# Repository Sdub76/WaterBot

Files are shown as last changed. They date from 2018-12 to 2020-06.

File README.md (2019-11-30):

# WaterBot 2
Christmas Tree Watering Robot 
Tree Watering Robot created to keep the Christmas tree wet without having to refill it everyday.  

## Features
1.  Monitor tree water level
2.  Monitor supply water level
3.  Pump water when tree water is low
4.  Only allow a maximum pump-on period per pumping session to avoid a HW or SW bug flooding the living room
5.  Give visual indication (via light on tree) that the pump is running
6.  Give visual indication (via light on tree) that the supply is empty
7.  Give visual indication (via light on tree) that there's a hardware fault
9.  Provide local debugging via OLED screen 
10.  (TBD) Log data via MQTT (Wi-fi) to see if things are working

Version 2 description TBD - Breadboard replaced by PCB, Crappy soil moisture sensor replaced with IR water sensor

## Shopping List
* TBD

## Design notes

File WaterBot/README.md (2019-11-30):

# WaterBot
ESP8266-based Tree Water Monitor
Tree Watering Robot created to keep the Christmas tree wet without having to refill it everyday.  

(https://youtu.be/NFjdOTcmyZQ "Click to Play in YouTube")

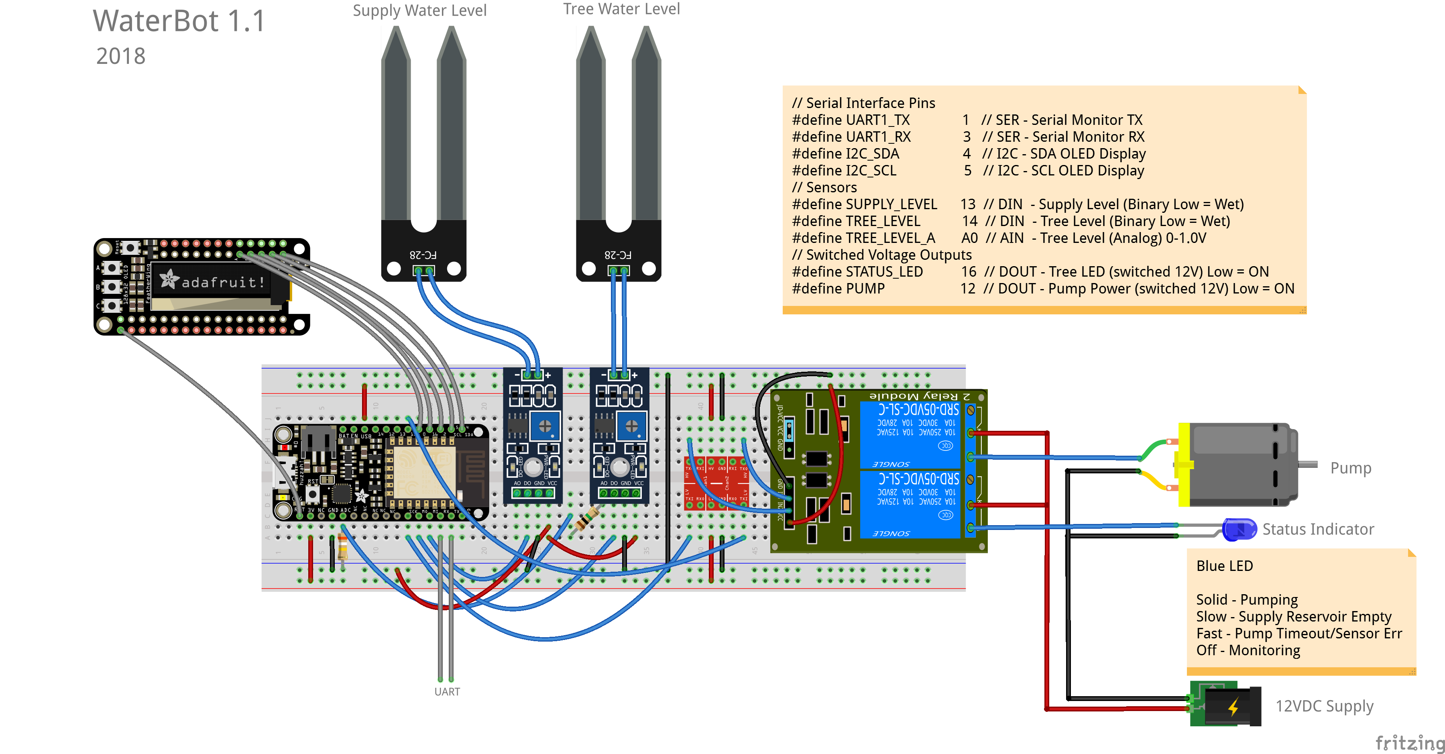
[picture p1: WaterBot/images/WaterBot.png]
Fritizing Image


## Features
1.  Monitor tree water level
2.  Monitor supply water level
3.  Pump water when tree water is low
4.  Only allow a maximum pump-on period per pumping session to avoid a HW or SW bug flooding the living room
5.  Give visual indication (via light on tree) that the pump is running
6.  Give visual indication (via light on tree) that the supply is empty
7.  Give visual indication (via light on tree) that there's a hardware fault
8.  (Disabled) Only turn on tree sensors when periodic readings are taking place to avoid sensor degradation via electrolysis
9.  Provide local debugging via OLED screen 
10.  (TBD) Log data via MQTT (Wi-fi) to see if things are working

NOTE: The original intent was to excite the tree level sensors with a digital output pin of the controller, so that the "on" time would be minimized, thus prolonging the life of the sensor probes.  The sensor probes electrolyze the water and erode the contacts when they're energized... thus you should only turn them on for a brief period if you're only taking periodic readings.  Unfortunately, I didn't have any spare GPIO pins on the ESP that weren't also used for bootloader control, so I commented out this code.  I suppose the sensors will work fine for a few weeks during the holiday season :)

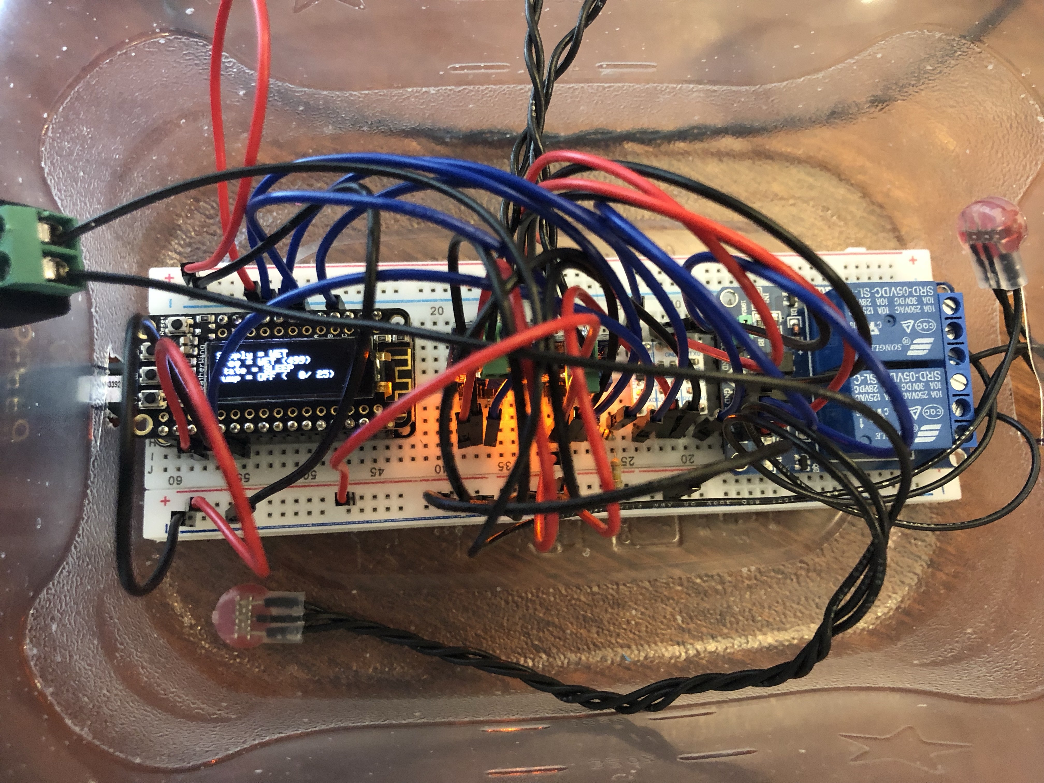
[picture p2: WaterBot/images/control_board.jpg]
Control Board

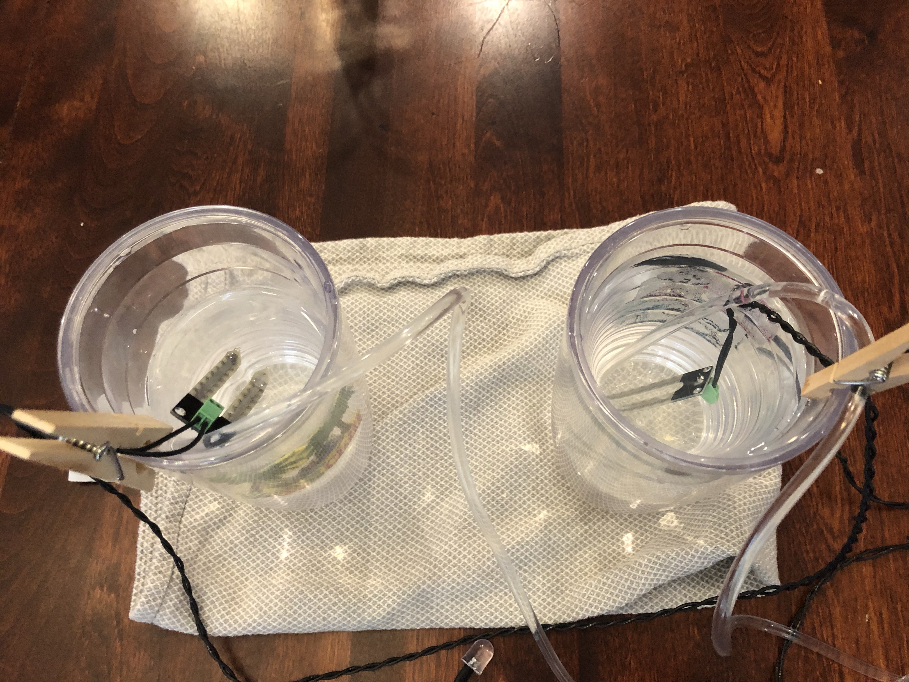
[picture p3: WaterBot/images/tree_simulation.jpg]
Tree Simulation


## Shopping List
* 1	Adafruit Feather HUZZAH ESP8266	part # [Adafruit #2821](https://www.adafruit.com/product/2821)
* 1	Adafruit OLED FeatherWing	part # [Adafruit #2900](https://www.adafruit.com/product/2900)
* 2	FC-28 Soil Hygrometer Module/Probe (http://a.co/d/3ILjnXG)
* 1	12VDC Diaphram pump	(http://a.co/d/7KirTrF)
* 1	Logic Level Converter	(https://www.microcenter.com/product/476364/velleman-33v-5v-ttl-logic-level-converter-module)
* 1	2-Channel 5v Relay Module (http://a.co/d/bQ4BVRI)
* 1	12VDC Power Supply (http://a.co/d/5liJUTH)
* 1	Blue (430nm) LED
* 1 220Ω Resitor for LED
* 1	1MΩ Resistor for Analog input voltage divider
* 1	390kΩ Resistor for Analog input voltage divider

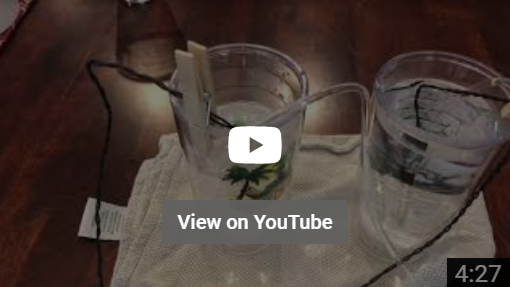
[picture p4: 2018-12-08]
WaterBot/images/youtube_thumb.png

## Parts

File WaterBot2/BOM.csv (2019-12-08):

RefDes | Quantity | Manufacturer | Function | Cost
C3 | 1 | CAP400 10uF | Power decouple | $0.04
C4 | 1 | CAP400 10uF | Power decouple | $0.04
C6 | 1 | CAP400 100nF | Sensor decouple | $0.04
C7 | 1 | CAP400 100nF | Sensor decouple | $0.04
C8 | 1 | CAP400 100nF | Sensor decouple | $0.04
D1 | 1 | LED Red | Power LED | $0.25
D2 | 1 | LED Blue | Tree Switch LED | $0.25
D3 | 1 | LED Blue | Tree Sensor LED1 | $0.25
D4 | 1 | LED Blue | Tree Sensor LED2 | $0.25
D5 | 1 | LED Blue | Tree Sensor LED3 | $0.25
D6 | 1 | LED Blue | Tree Sensor LED4 | $0.25
D7 | 1 | LED Blue | Supply Switch LED | $0.25
J1 | 1 | HDR-1x6 | Pro mini FTDI opt.
J2 | 1 | Molex 395021006 | SPI LED out | $1.40
J3 | 1 | Molex 395021002 | Lamp conn | $0.58
J4 | 1 | HDR-1x3 | Lamp relay out opt.
J5 | 1 | HDR-1x3 | Pump relay out opt.
J6 | 1 | Molex 395021002 | Pump conn | $0.58
J7 | 1 | Molex 395021003 | Supply switch in | $0.78
J8 | 1 | CUI PJ-002A | 12V barrel jack | $0.70
J9 | 1 | Molex 395021003 | Tree Sensor in | $0.78
J10 | 1 | Molex 395021002 | 12V in opt. | $0.58
J11 | 1 | Molex 395021003 | Tree Switch in | $0.78
J12 | 1 | HDR-1x4 | Relay control opt.
M1 | 1 | ARDUINO-PRO-MINI-5.0V | Control CPU | $9.95
MS1 | 1 | Adafruit featherwing ESP8266 | Monitoring CPU | $19.95
R1 | 1 | RES400 (220 Ohm) | 5V Power LED Res | $0.10
R2 | 1 | RES400 (220 Ohm) | Tree Switch LED Res | $0.10
R3 | 1 | RES400 (220 Ohm) | Tree Sensor LED1 Res | $0.10
R4 | 1 | RES400 (220 Ohm) | Tree Sensor LED2 | $0.10
R5 | 1 | RES400 (220 Ohm) | Tree Sensor LED3 | $0.10
R6 | 1 | RES400 (220 Ohm) | Tree Sensor LED4 | $0.10
R10 | 1 | RES400 (220 Ohm) | Supply Switch LED | $0.10
U1 | 1 | 2SRD Relay Module | Mechanical relays | $1.86
U2 | 1 | LM3940 | 5->3.3V regulator | $1.63
U3 | 1 | 4ch i2c logic level module | 5<->3.3V level conv | $2.95
U4 | 1 | 78SRinv_horiz | 12->5V regulator | $4.30
 | 1 | WaterBot 2.0 PCB | PCB | $1.88
 | 1 | 12V Diaphram Pump | Water pump | $7.68
 | 1 | Water level sensor (IR) | Tree level sensor | $7.67
 | 1 | Water level switch (IR) | Tree level switch | $2.60
 | 1 | Water level switch (IR) | Water supply switch | $2.60
 | 1 | Adafruit featherwing OLED |  | $14.95
 | 1 | 12VDC power supply |  | $10.98
 | 37 |  |  | $97.82

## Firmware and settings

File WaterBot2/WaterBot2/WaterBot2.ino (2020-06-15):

/* WaterBot2
 *
 * Version 2.0 of Tree Watering Robot
 *       
 * Tree watering system
 * 
 * Place supply switch at bottom of water tank
 * Place Tree switch at level you wwant watering to begin
 * Place Tree level sensor in stand's float hole
 * 
 * If tree switch is higher than level sernsor, error will be reported
 * If tree switch is lower than level sensor, pump won't run until both are satisfied,
 *    but risk of pump timing out of it runs too long, since water level is very low.  
 *    Care must be taken to not allow water level to get undesirably low.
 *    
 * LCD displays and ESP8266 are optional
 * 
 * Water Level Sensor
 * https://www.amazon.com/gp/product/B07BFPP4TQ/ref=ppx_yo_dt_b_asin_title_o01_s00?ie=UTF8&psc=1
 * Water Switch
 * https://www.amazon.com/gp/product/B0811GRVJH/ref=ppx_yo_dt_b_asin_title_o01_s00?ie=UTF8&psc=1
 * Water Pump
 * https://www.amazon.com/gp/product/B0744FWNFR/ref=ppx_yo_dt_b_search_asin_title?ie=UTF8&psc=1
 * 
 * Issues: Pump needs flyback diodes
 * 
 */
#include <FreqMeasure.h>
#include "TimedBlink.h"



//PIN DEFINITIONS
#define PIN_SERIAL_TX      0
#define PIN_SERIAL_RX      1

#define PIN_SPI_MOSI      11
#define PIN_SPI_MISO      12
#define PIN_SPI_SCK       13
#define PIN_SPI_SS        17

#define PIN_TREE_SENSOR   14
#define PIN_LEVEL_SENSOR   8
#define PIN_SUPPLY_SENSOR  7

#define PIN_TREE_LED       2
#define PIN_LEVEL1_LED     6
#define PIN_LEVEL2_LED     5 
#define PIN_LEVEL3_LED     4
#define PIN_LEVEL4_LED     3
#define PIN_SUPPLY_LED     9

#define PIN_PUMP          15
#define PIN_LAMP          16

//Sensor characteristics (Hz)
#define WATER_LEVEL_0 20
#define WATER_LEVEL_1 50
#define WATER_LEVEL_2 100
#define WATER_LEVEL_3 200
#define WATER_LEVEL_4 400

//States
int     SupplyState = 0;
int     TreeState = 0;
#define SENSOR_WET 0
#define SENSOR_DRY 1
#define SENSOR_ERR 2

int     PumpState = 0;
#define PUMP_OFF 0
#define PUMP_ON  1
#define PUMP_ERR 2

//Other parameters
#define AVERAGE_LENGTH 30  // Number of points to average for frequnecy calc
#define PUMP_MAXTIME   10  // Number of seconds to allow pump to run

double sum = 0;
int count = 0;
double frequency = 0;
unsigned long prev_time_freq = 0;
unsigned long prev_time_ser = 0;

//Inputs
int SupplySwitch = 0;
int TreeSwitch = 0;
unsigned long TreeLevel = 0;

// TIming state vars
unsigned long current_time = 0;
double timeout = 0;
double PumpStart = 0;

TimedBlink level1_led(PIN_LEVEL1_LED);
TimedBlink level2_led(PIN_LEVEL2_LED);
TimedBlink level3_led(PIN_LEVEL3_LED);
TimedBlink level4_led(PIN_LEVEL4_LED);
TimedBlink status_lamp(PIN_LAMP);

void setup() {

  Serial.begin(57600);
  Serial.println("Serial Initialized");

  // Intialize Inputs
  pinMode(PIN_TREE_SENSOR,INPUT);
  pinMode(PIN_LEVEL_SENSOR,INPUT);
  pinMode(PIN_SUPPLY_SENSOR,INPUT_PULLUP);

  // Intialize Outputs
  pinMode(PIN_TREE_LED,OUTPUT);
  pinMode(PIN_LEVEL1_LED,OUTPUT);
  pinMode(PIN_LEVEL2_LED,OUTPUT);
  pinMode(PIN_LEVEL3_LED,OUTPUT);
  pinMode(PIN_LEVEL4_LED,OUTPUT);
  pinMode(PIN_SUPPLY_LED,OUTPUT);
  pinMode(PIN_PUMP,OUTPUT);
  pinMode(PIN_LAMP,OUTPUT);
  level1_led.blink(50,50);
  level2_led.blink(50,50);
  level3_led.blink(50,50);
  level4_led.blink(50,50);
  
  FreqMeasure.begin();

  timeout = AVERAGE_LENGTH/(WATER_LEVEL_0*0.9);

}


void loop() {

  current_time = millis();

  ReadInputs();

  UpdateStates();

  WriteOutputs();

  UpdateDisplays();
  
  LogData();

  if ((current_time - prev_time_ser) > 2000) {

    DebugOutputs();
    prev_time_ser = current_time;
  }

}


void ReadInputs() {
  //Read Sensors
  
  SupplySwitch = digitalRead(PIN_SUPPLY_SENSOR);
  
  TreeSwitch = digitalRead(PIN_TREE_SENSOR);

  if (FreqMeasure.available()) {
    // average several reading together
    sum = sum + FreqMeasure.read();
    count = count + 1;
    if (count > AVERAGE_LENGTH) {
      // Reset timer
      prev_time_freq = current_time;
      frequency = FreqMeasure.countToFrequency(sum / count);
      sum = 0;
      count = 0;
      TreeLevel = 0;
      if (frequency > (WATER_LEVEL_0*0.9)) TreeLevel++;
      if (frequency > (WATER_LEVEL_1*0.9)) TreeLevel++;
      if (frequency > (WATER_LEVEL_2*0.9)) TreeLevel++;
      if (frequency > (WATER_LEVEL_3*0.9)) TreeLevel++;
      if (frequency > (WATER_LEVEL_4*0.9)) TreeLevel++;
    }
  }
//  if ((current_time - prev_time_freq) > timeout) {
//     TreeLevel = 0;
//     Serial.println("timeout");
//  }

}

void UpdateStates() {
  //Update States
  
  if (SupplySwitch == 0) {
    SupplyState = SENSOR_WET; // Low = Wet
  } else {
    SupplyState = SENSOR_DRY;
  }

  // Fuse TreeSwitch and TreeLevel into TreeState
  // ToDo: Add hysteresis
  if (TreeLevel == 0) {         // Sensor Timeout
    TreeState = SENSOR_ERR; 
  } else if (TreeSwitch == 0) { // Low = Wet (regardless of level sensor)
    TreeState = SENSOR_WET; 
  } else if (TreeLevel < 5) {  // Sensor Less than full and Switch = Dry
    TreeState = SENSOR_DRY; 
  } else {
    TreeState = SENSOR_ERR;   // Sensor Full & Switch Dry conflict -- Bad switch placement?
  }
  // Fuse TreeState and SwitchState into PumpState
  switch (PumpState) {
    case PUMP_OFF :
      if ((TreeState == SENSOR_DRY) && (SupplyState == SENSOR_WET)) {
        PumpStart = current_time; // Record pumping start time
        PumpState = PUMP_ON;
      }
      break;
    
    case PUMP_ON :
      // If TreeState or Supply State change, stop pumping
      if ((TreeState != SENSOR_DRY) || (SupplyState != SENSOR_WET)) {
        PumpState = PUMP_OFF;
      }
      
      if ((current_time - PumpStart) > PUMP_MAXTIME*1000) {
        PumpState = PUMP_ERR;
      }
      break;

    case PUMP_ERR :
      // Do nothing until power cycle
      // Todo: Add auto-reset sequence? Allow pumping as long as positive level progress being made?
    break;
  }
}

void WriteOutputs() {
  // Update Pump output
  if (PumpState == PUMP_ON) {
    digitalWrite(PIN_PUMP,false);
  } else {
    digitalWrite(PIN_PUMP,true);
  }

  // Update remote status lamp (in order of importance)
  // Note relay is active low, so "on" is really "off" in the blink routine
  //
  // Fast Blink = Sensor Error (Either Level=0Hz or Switch Dry while Level OK)
  // On Blip = Pump Lockout (Pump ran too long)
  // Off Blip = Supply Empty
  // Slow Blink = Pump On
  // On = Standby
  if (TreeState == SENSOR_ERR) {
    status_lamp.blink(50,50); 
  } else if (PumpState == PUMP_ERR) {
    status_lamp.blink(2000,50);
  } else if (SupplyState == SENSOR_DRY) {
    status_lamp.blink(50,2000);
  } else if (PumpState == PUMP_ON) {
    status_lamp.blink(1000,1000);
  } else {
    status_lamp.on();
  }
  
  // Update LEDs
  if (SupplySwitch == SENSOR_WET) {
    digitalWrite(PIN_SUPPLY_LED,true);
  } else {
    digitalWrite(PIN_SUPPLY_LED,false);
  }
  
  if (TreeSwitch == SENSOR_WET) {
    digitalWrite(PIN_TREE_LED,true);
  } else {
    digitalWrite(PIN_TREE_LED,false);
  }
  
  switch (TreeLevel) {
    case 0:
      level1_led.blink();
      level2_led.blink();
      level3_led.blink();
      level4_led.blink();
      break;
    case 1:
      level1_led.off();
      level2_led.off();
      level3_led.off();
      level4_led.off();
      break;
    case 2:
      level1_led.off();
      level2_led.off();
      level3_led.off();
      level4_led.on();
      break;
    case 3:
      level1_led.off();
      level2_led.off();
      level3_led.on();
      level4_led.on();
      break;
    case 4:
      level1_led.off();
      level2_led.on();
      level3_led.on();
      level4_led.on();
      break;
    case 5:
      level1_led.on();
      level2_led.on();
      level3_led.on();
      level4_led.on();
      break;
  }

}

void UpdateDisplays() {
  //ToDo: Drive I2C display directly -OR- Send to ESP8266 via UART
  //ToDo: Send SPI LCD commands (Alternative to lamp... 2020 enhancement)
}

void LogData() {
  //ToDo: Send data to ESP8266 for MQTDD logging (2020 enhancement)
}

void DebugOutputs() {

  Serial.println("==INPUTS==");
  Serial.print(" SupplySwitch = ");
  switch (SupplySwitch) {
    case SENSOR_WET : 
    Serial.println("WET");
    break;

    case SENSOR_DRY : 
    Serial.println("DRY");
    break;
    
    case SENSOR_ERR : 
    Serial.println("ERROR");
    break;
  }
  Serial.print(" TreeSwitch = ");
  switch (TreeSwitch) {
   case SENSOR_WET : 
    Serial.println("WET");
    break;

    case SENSOR_DRY : 
    Serial.println("DRY");
    break;
    
    case SENSOR_ERR : 
    Serial.println("ERROR");
    break;
  }
  Serial.print(" TreeLevel = ");
  Serial.print(TreeLevel);
  Serial.print(" (");
  Serial.print(frequency);
  Serial.println("Hz)");

  Serial.println("==STATES==");
  Serial.print(" SupplyState = ");
  switch (SupplyState) {
    case SENSOR_WET : 
    Serial.println("WET");
    break;

    case SENSOR_DRY : 
    Serial.println("DRY");
    break;
    
    case SENSOR_ERR : 
    Serial.println("ERROR");
    break;
  }
  Serial.print(" TreeState = ");
  switch (TreeState) {
    case SENSOR_WET : 
    Serial.println("WET");
    break;

    case SENSOR_DRY : 
    Serial.println("DRY");
    break;
    
    case SENSOR_ERR : 
    Serial.println("ERROR");
    break;
  }
  Serial.print(" PumpState = ");
  switch (PumpState) {
    case PUMP_OFF : 
    Serial.println("OFF");
    break;

    case PUMP_ON : 
    Serial.print("ON (");
    Serial.print((current_time-PumpStart)/1000);
    Serial.println("s)");
    break;
    
    case PUMP_ERR : 
    Serial.println("ERROR");
    break;
  }
  
  Serial.println("");
  
}

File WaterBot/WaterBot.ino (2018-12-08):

// WaterBot
// Christmas Tree Watering Bot
//  

#include <SPI.h>
#include <Wire.h>
#include <Adafruit_GFX.h>
#include <Adafruit_SSD1306.h>

/////////////////////////
// Macro Definition
/////////////////////////
// Printing with stream operator
template<class T> inline Print& operator <<(Print &obj,     T arg) { obj.print(arg);    return obj; }
template<>        inline Print& operator <<(Print &obj, float arg) { obj.print(arg, 4); return obj; }

/////////////////////////
// HARDWARE DEFINITION
/////////////////////////
// Serial Interface Pins
#define UART1_TX          1   // SER - Serial Monitor TX
#define UART1_RX          3   // SER - Serial Monitor RX
#define I2C_SDA           4   // I2C - SDA OLED Display
#define I2C_SCL           5   // I2C - SCL OLED Display
// Sensors
//#define SENSOR_EXCITATION 15  // DOUT - Level Sensor Excitation / Red LED  
#define SUPPLY_LEVEL      13  // DIN  - Supply Level (Binary Low = Wet)
#define TREE_LEVEL        14  // DIN  - Tree Level (Binary Low = Wet)
#define TREE_LEVEL_A      A0  // AIN  - Tree Level (Analog) 0-3.3V through 390/1M Voltage Divider = 0.00-0.93V
// Switched Voltage Outputs
#define STATUS_LED        16  // DOUT - Tree LED (switched 12V) Low = ON 
#define PUMP              12  // DOUT - Pump Power (switched 12V) Low = ON
// SPECIAL FUNCTION PINS
#define GPIO0             0   // BOOTLOADER - BOOT SKETCH - Red LED (Don't use for other purpose)
#define GPIO2             2   // BOOTLOADER - UART BOOTLOADER - Blue LED (Don't use for other purpose)
#define GPIO15            15  // BOOTLOADER - SDIO MODE

//VARIABLE DEFINITION
unsigned long LoopTimer = 0;  // Timer variable for major frames
int LoopDelay = 5000;         // Delay between major frames (ms)

unsigned long BlinkTimer = 0; // Timer variable for LED Blink
int LED_State  = 0;           // State variable for LED
int BlinkDelay = 0;           // Delay between LED state changes (ms)
#define LED_OFF           0   // Steady OFF
#define LED_ON           -1   // Steady ON
#define LED_SLOW        500   // Time between slow LED toggles
#define LED_FAST         50   // Time between fast LED toggles

#define RELAY_OFF         1   // SVO Relay is active LOW
#define RELAY_ON          0   // SVO Relay is active LOW

unsigned long TimePrev = 0;   // State variable for pump timer
unsigned long TimeCurr = 0;   // Current Time for pump timer
bool NewPumpSession = true;   // Flag to indicate transition to new pumping session
int PumpTime = 0;             // Accumlated watering time this pumping session (ms)
int PumpTimeout = 10*1000;    // Maximum allowable pump run time (ms)
float WaterTime = 0.0;        // Accumulated total watering time (s)
int Pump_State = 0;           // State variable for Pump

int SupplyState = 0;          // Digital Supply level sensor value
int TreeState_raw = 0;        // Digital Tree level sesor value        
int TreeLevel_raw = 0;        // Analog Tree level sensor value
int TreeState = -1;           // Post-processed tree level state
float TreeLevel = 0.0;        // Post-processed tree level value (0-100%)

#define SENSOR_WET         0  // Water level sensor is low = wet
#define SENSOR_DRY         1  // Water level sensor is high = dry
#define SENSOR_ERROR      -1  // Water level sensor is invalid

#define SENS_RAW_EMPTY   725  // Based on manual calibration (raw ADC counts)
#define SENS_RAW_FULL    320  // Based on manual calibration (raw ADC counts)
#define SENS_RAW_ERR     900  // Based on manual calibration (raw ADC counts)

int State = 0;                // Main Control State Variable
#define STATE_SLEEP      0    // Sleep
#define STATE_RUN        1    // Running/Filling
#define STATE_LOWSUPPLY  2    // Supply reservoir empty
#define STATE_SENSORERR  3    // Sensor out of range
#define STATE_FAILSAFE   4    // Failsafe state if pump runs too long

/////////////////////////
//STRUCT Initialization
/////////////////////////
Adafruit_SSD1306 display = Adafruit_SSD1306(128, 32, &Wire);



void setup() {

  // Initialize Outputs
  pinMode(PUMP, OUTPUT);
  digitalWrite(PUMP,RELAY_OFF);
  pinMode(STATUS_LED, OUTPUT);
  digitalWrite(STATUS_LED,RELAY_OFF);
//  pinMode(SENSOR_EXCITATION, OUTPUT);

  // Initialize Inputs
  pinMode(SUPPLY_LEVEL, INPUT);
  pinMode(TREE_LEVEL, INPUT);
  pinMode(TREE_LEVEL_A, INPUT);


  // Begin Serial Debug Interface
  Serial.begin(9600);
  Serial.println("WaterBot Serial Monitor");

  // Begin OLED Display Interface
  // SSD1306_SWITCHCAPVCC = generate display voltage from 3.3V internally
  // Address 0x3C for 128x32
  display.begin(SSD1306_SWITCHCAPVCC, 0x3C);
  display.display(); // Display splashscreen
  delay(1000);
  display.clearDisplay();
  display.display();
  display.setTextSize(1);
  display.setTextColor(WHITE);
  display.setCursor(0,0);

  // Initalize Variables
  State = STATE_RUN;       // Initialize Control State to Running
  Pump_State = LOW;        // Initialize Pump to OFF
  LED_State = RELAY_OFF;         // Initialize LED to OFF
  LoopTimer = millis();    // Initialize Loop timer
  BlinkTimer = millis();   // Initialize LED timer

}

// TODO Add MQTT Reporting
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

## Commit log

2019-11-30 Created WaterBot2 PCB
    [BoardOutline.gbr, Bottom.gbr, BottomAssy.gbr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]
2019-11-30 Minor Updates, Added BOM
    [BOM.csv]
2019-12-02 Added pin mapping
2019-12-08 Fixed errors found in initial commission
    [WaterBot2.ino]
